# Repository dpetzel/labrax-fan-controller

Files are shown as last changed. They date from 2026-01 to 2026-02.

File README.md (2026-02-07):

# Lab Rax Cooling Fan Controller
As Homelab Upgrade 2026 progress, I've gotten to a point
where I want to install a fan in my Lab Rax mini rack.

This turned out to be a bigger adventure than I expected
and throughout the process I collected a bunch of information 
that I will never remember, so I've captured my notes.

While I'm focused on my Lab Rax build this setup should
work in any number of situations

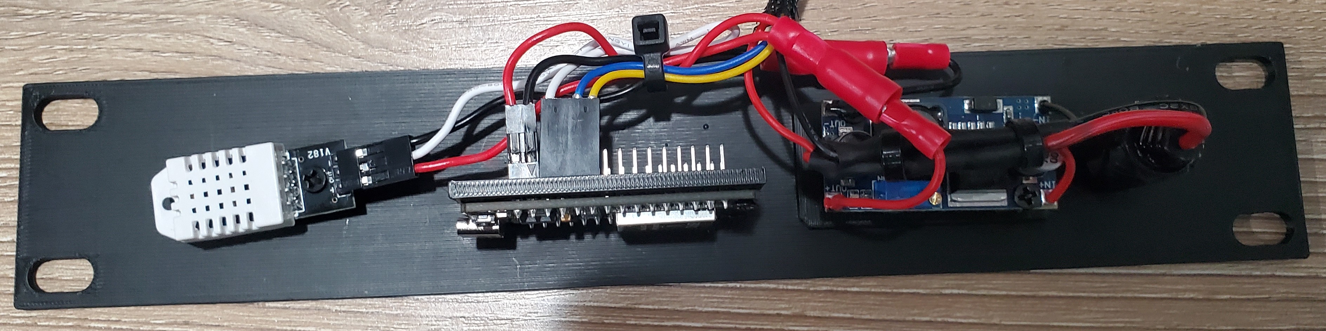
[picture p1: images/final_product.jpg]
Final Product


## Components

<table>
  <thead>
    <th>Component</th>
    <th>Source</th>
    <th>Thumbnail</th>
  </thead>
  <tbody>
    <tr>
      <td>ESP32</td>
      <td>
        <a href="https://www.amazon.com/dp/B0CR5Y2JVD?th=1">Amazon</a>
      </td>
      <td>
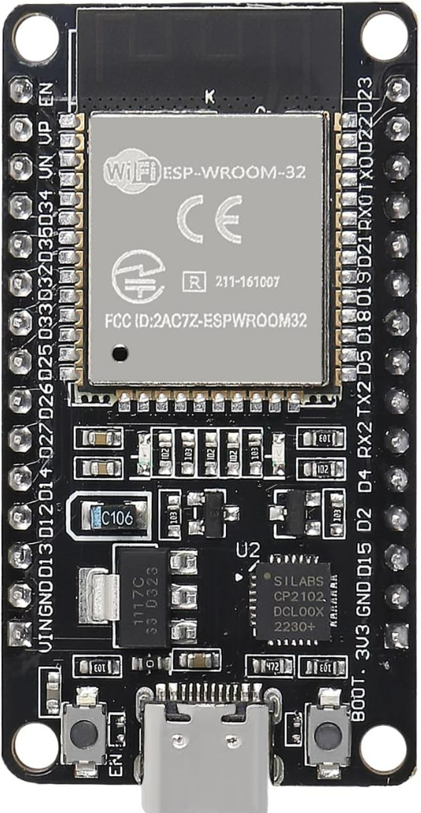
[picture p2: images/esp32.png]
        
      </td>
    </tr>
    <tr>
      <td>12v Buck Converter</td>
      <td>
        <a href="https://www.amazon.com/dp/B0DBVYP91F?ref=ppx_yo2ov_dt_b_fed_asin_title&th=1">Amazon</a>
      </td>
      <td>
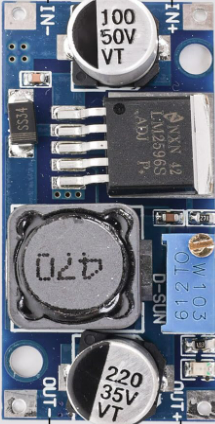
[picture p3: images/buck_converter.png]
        
      </td>
    </tr>
    <tr>
      <td>DHT22</td>
      <td>
        <a href="https://www.amazon.com/dp/B0FK5K45KF">Amazon</a>
      </td>
      <td>
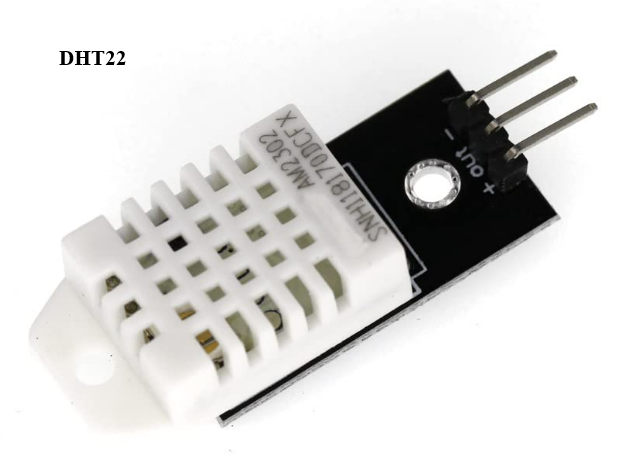
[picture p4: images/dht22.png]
        
      </td>
    </tr>
    <tr>
      <td>120mm Fan</td>
      <td>
        <a href="https://www.amazon.com/dp/B0DJDC74BP">Amazon</a>
      </td>
      <td>
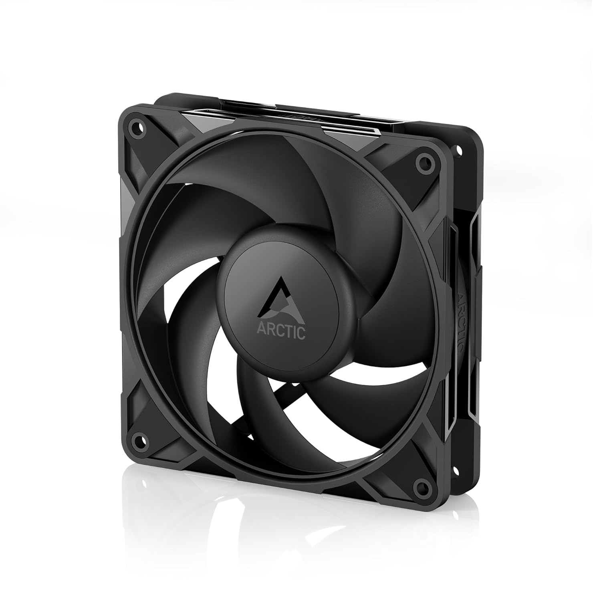
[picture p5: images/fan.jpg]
        
      </td>
    </tr>
    <tr>
      <td>12v Barrel Connector</td>
      <td>
        <a href="https://www.amazon.com/dp/B0D8BDX6Q5?th=1">Amazon</a>
      </td>
      <td>
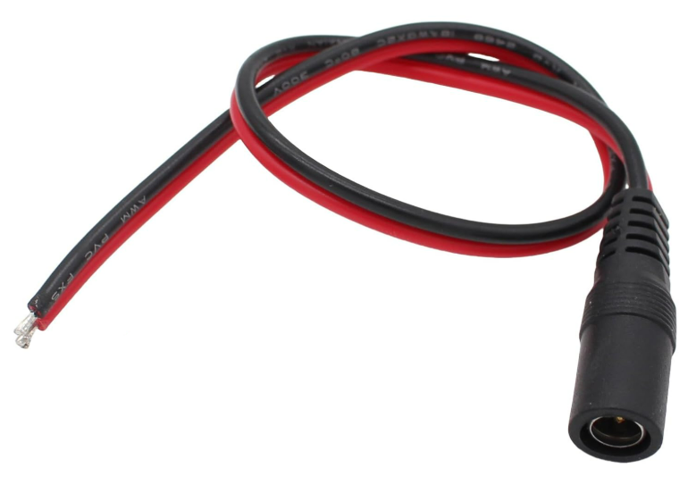
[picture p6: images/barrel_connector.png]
        
      </td>
    </tr>
  </tbody>
</table>

## Power Budget
Assuming an 85% buck efficiency

| Component | Voltage | Current (Max) | 12V Input Current (Max) |
| --- | --- | --- | --- |
| ESP32 | 3.3V | 0.50 A | 0.16 A |
| Fan | 12V | 0.33 A | 0.33 A |
| DHT22 | 3.3 V | 0.0025 A | 0.0007 A |
| | | | |
| **Total** | | | **0.49 A** |

## Wiring
### Diagram
```mermaid
flowchart TD
    subgraph ESP32
        esp_33[3.3V +]
        esp_gnd[Gnd]
        esp13[GPIO 13]
        esp14[GPIO 14]
    end

    subgraph ps[12V Power Suppy]
        12v+[+]
        12v-[Gnd]
    end
    110v[110v AC] <--> ps

    subgraph DHT22
        dht+[3.3V +]
        dht-[Gnd]
        dhtData[Data]
    end

    subgraph buck[Buck Converter]
        buckIn+[+ in]
        buckIn-[Gnd in]
        buckOut+[3.3V + Out]
        buckOut-[Gnd out]
    end

    subgraph Fan
        fan+[+]
        fan-[Gnd]
        fanTach[Tach]
        fanPmw[PMW]
    end

    dhtData <--> esp13

    fanPmw <--> esp14

    12v+ <--> buckIn+
    12v- <--> buckIn-

    fan+ <--> 12v+
    fan- <--> 12v-

    dht+ <--> buckOut+
    dht- <--> buckOut-

    esp_33 <--> buckOut+
    esp_gnd <--> buckOut-
```

## 3D Printed Custom Mount
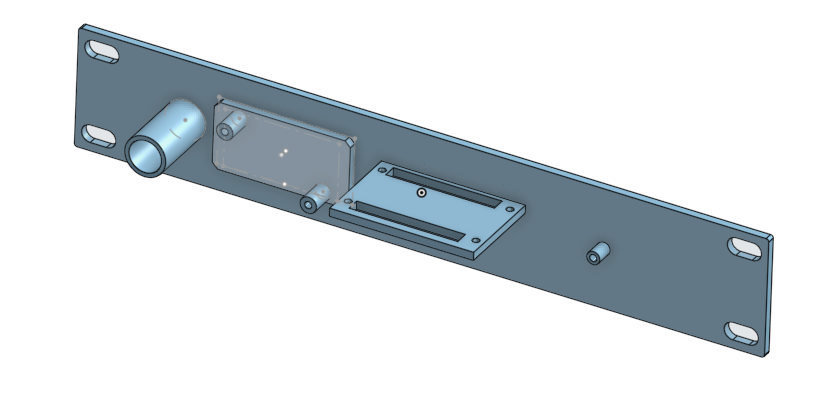
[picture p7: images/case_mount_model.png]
Custom Mount


[STL File](./Fan%20Controller%20-%20Mini%20Rack%20Mount.stl)

[Step File](./Fan%20Controller%20-%20Mini%20Rack%20Mount.step)

[onshape](https://cad.onshape.com/documents/b9def82ccf3bdff9cf5f2438/w/35c5b6c4bbd6ace056f11a3f/e/4fe5b528b247836f305f482f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)

## Code
See [RackFanWithTempSensorv1.ino](./RackFanWithTempSensorv1.ino)

## ESP32 Pinout
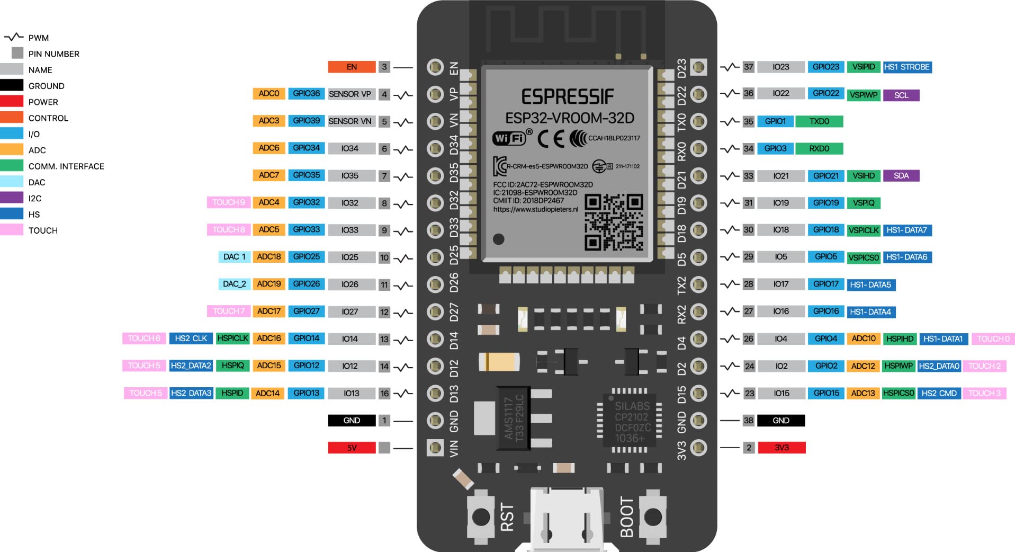
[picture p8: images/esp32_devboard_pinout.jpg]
ESP32 Pinout


## References
Here are a few references I leveraged along the way.
* https://esp32io.com/tutorials/esp32-dht22
* https://randomnerdtutorials.com/esp32-dht11-dht22-temperature-humidity-sensor-arduino-ide/
* https://dronebotworkshop.com/esp32-pwm-fan/

## Notes & Observations

Avoid `GPIO12`- This is tied in with the flashing process. Everything will work fine
through the flashing process and you won't suspect a thing until you physically power
cycle the device. At that point it just gets into a reboot loop. I ran into this 
when it was attached to fan PWM. Unclear if similar problems on other functionality.

Tachometer was not reliable. It would only properly record when fan duty was at 100%.
This was fine as I don't actually need to monitor RPMs and I only discovered this
while playing around

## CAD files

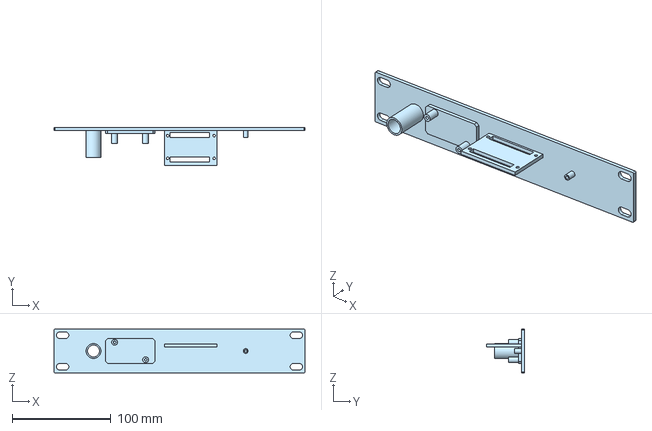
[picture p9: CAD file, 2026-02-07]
Fan Controller - Mini Rack Mount.step
254.0 x 38.0 x 44.5 mm

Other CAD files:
Fan Controller - Mini Rack Mount.stl

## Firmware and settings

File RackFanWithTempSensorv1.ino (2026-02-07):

#include <DHT.h>

// PWM settings
const int PWM_FREQ = 25000;    // 25 kHz frequency for computer fans
const int PWM_RESOLUTION = 8;  // 8-bit resolution (0-255)

// Pin definitions 
#define PWM_PIN 14 // Attached to the Fan's PWM terminal for speed control
#define DHT22_PIN 13 // Attached to the DT22 Sensor's Data Pin
#define ONBOARD_LED_PIN 2 // The onboard LED is tied to GPIO2
#define TACH_PIN 27 //Unused

#define LOOP_DELAY_MS 2000 // How long to wait between each polling loop
#define LED_PERIOD_MS 50 // How long should the onboard LED remain on each polling loop

// When the temperature is below this value
// the fan will be turned off
const float TEMP_LOW_THRESHOLD_CELSIUS = 32;

// Kick the fan to 100% over this threshold
const float TEMP_HIGH_THRESHOLD_CELSIUS = 38;

DHT dht22(DHT22_PIN, DHT22);

void setFanSpeed(int percent) {
  if (percent < 0) percent = 0;
  if (percent > 100) percent = 100;

  int maxDuty = (1 << PWM_RESOLUTION) - 1;
  int duty = (percent * maxDuty) / 100;

  ledcWrite(PWM_PIN, duty);
}

void setup() {
  Serial.begin(115200);
  dht22.begin();

  // pinMode(TACH_PIN, INPUT_PULLUP);
  pinMode(ONBOARD_LED_PIN, OUTPUT);

  // Configure PWM
  ledcAttach(PWM_PIN, PWM_FREQ, PWM_RESOLUTION);
  setFanSpeed(0);

  delay(1000);
  Serial.println("System ready!"); 
}

void loop() {
  // Flip the LED on to indicate we are doing some work.
  digitalWrite(ONBOARD_LED_PIN, HIGH);  // LED ON

  float humi  = dht22.readHumidity();
  float tempC = dht22.readTemperature();
  float tempF = tempC * 9.0 / 5.0 + 32.0;

  if (tempC <= TEMP_LOW_THRESHOLD_CELSIUS) {
    Serial.println("Turning off Fan");
    setFanSpeed(0);
  } else if (tempC >= TEMP_HIGH_THRESHOLD_CELSIUS) {
    Serial.println("Setting fan to max!");
    setFanSpeed(100);
  } else {
    Serial.println("Turning on Fan");
    setFanSpeed(25);
  }

  Serial.print("Humidity: ");
  Serial.print(humi);
  Serial.print("%");

  Serial.print("  |  ");

  Serial.print("Temperature: ");
  Serial.print(tempC);
  Serial.print("°C  ~  ");
  Serial.print(tempF);
  Serial.println("°F");

  delay(LED_PERIOD_MS);
  // Turn off the onboard LED
  digitalWrite(ONBOARD_LED_PIN, LOW);
  delay(LOOP_DELAY_MS);
}

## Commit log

2026-01-30 Wiring Diagram
2026-01-30 Fix ESP voltage
2026-01-31 add main power
2026-02-07 controller mount
    [Fan Controller - Mini Rack Mount.step, Fan Controller - Mini Rack Mount.stl]
2026-02-07 add the barrel connector
